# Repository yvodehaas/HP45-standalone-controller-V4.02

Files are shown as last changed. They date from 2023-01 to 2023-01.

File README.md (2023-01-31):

# HP45-standalone-controller-V4.02
HP45 standalone controller V4.02

This github repository is a direct upload of the HP45 Standalone controller V4.02.

This version uses a Teensy 3.5, has all the extra circuits to use DMA for inkjet, and has self testing capabilities. 
A more detailed set of information can be found here: https://ytec3d.com/hp45-controller-v4/

The firmware to run on this board is found here: https://github.com/yvodehaas/HP45-standalone-V4
And the software to control it is found here: https://github.com/yvodehaas/Inkjet-commander
Oasis controller also works on this controller, though it will only work in an Oasis based machine: https://hackaday.io/project/86954-oasis-3dp

This project has been discontinued on my side and is uploaded in the hope that someone else can use it as a template or as is. It is provided without warranty.

The board has a few known issues to keep in mind:
- The reset pulse circuit that resets the TLC59213 using the 74HC123 NEEDS to work. Without this the TLC59213 stays powered. Best case this destroys the HP45 nozzles on the HP45, works case it first destroys the TLC59213, then the Teensy 3.5
- The TLC59213 has a direct connection to the Teensy 3.5. The TLC59213 breaking usually applies the 12V supply to the Teensy 3.5 pins, destroying it.
- The Address testing circuit sometimes gives false negatives. The controller will still print, but while throwing errors.
- The resistor accross the 4017 and 4081 circuit (address circuit) is there to raise the voltage for the nozzle check circuit. The HP45 has pulldown resistors that lowered the voltage on the test circuit sufficiently to stop being able to test.
- Temperature is an indication. The formula was based on 2 printheads while it is known that the HP45 has no accurate temperature sensor. 80C at startup is possible.
- The controller needs 3 pulses to fire all nozzles in an address. This is done 5 primitives, 5 primitives and 4 primitives on each address. This seems to be an issue in the HP45, where too much heat builds up, leading to misfirings. Varying the voltage on the VHD should make this better, but this needs to be calibrated for each printhead.

This list will get appended when more issues are found.

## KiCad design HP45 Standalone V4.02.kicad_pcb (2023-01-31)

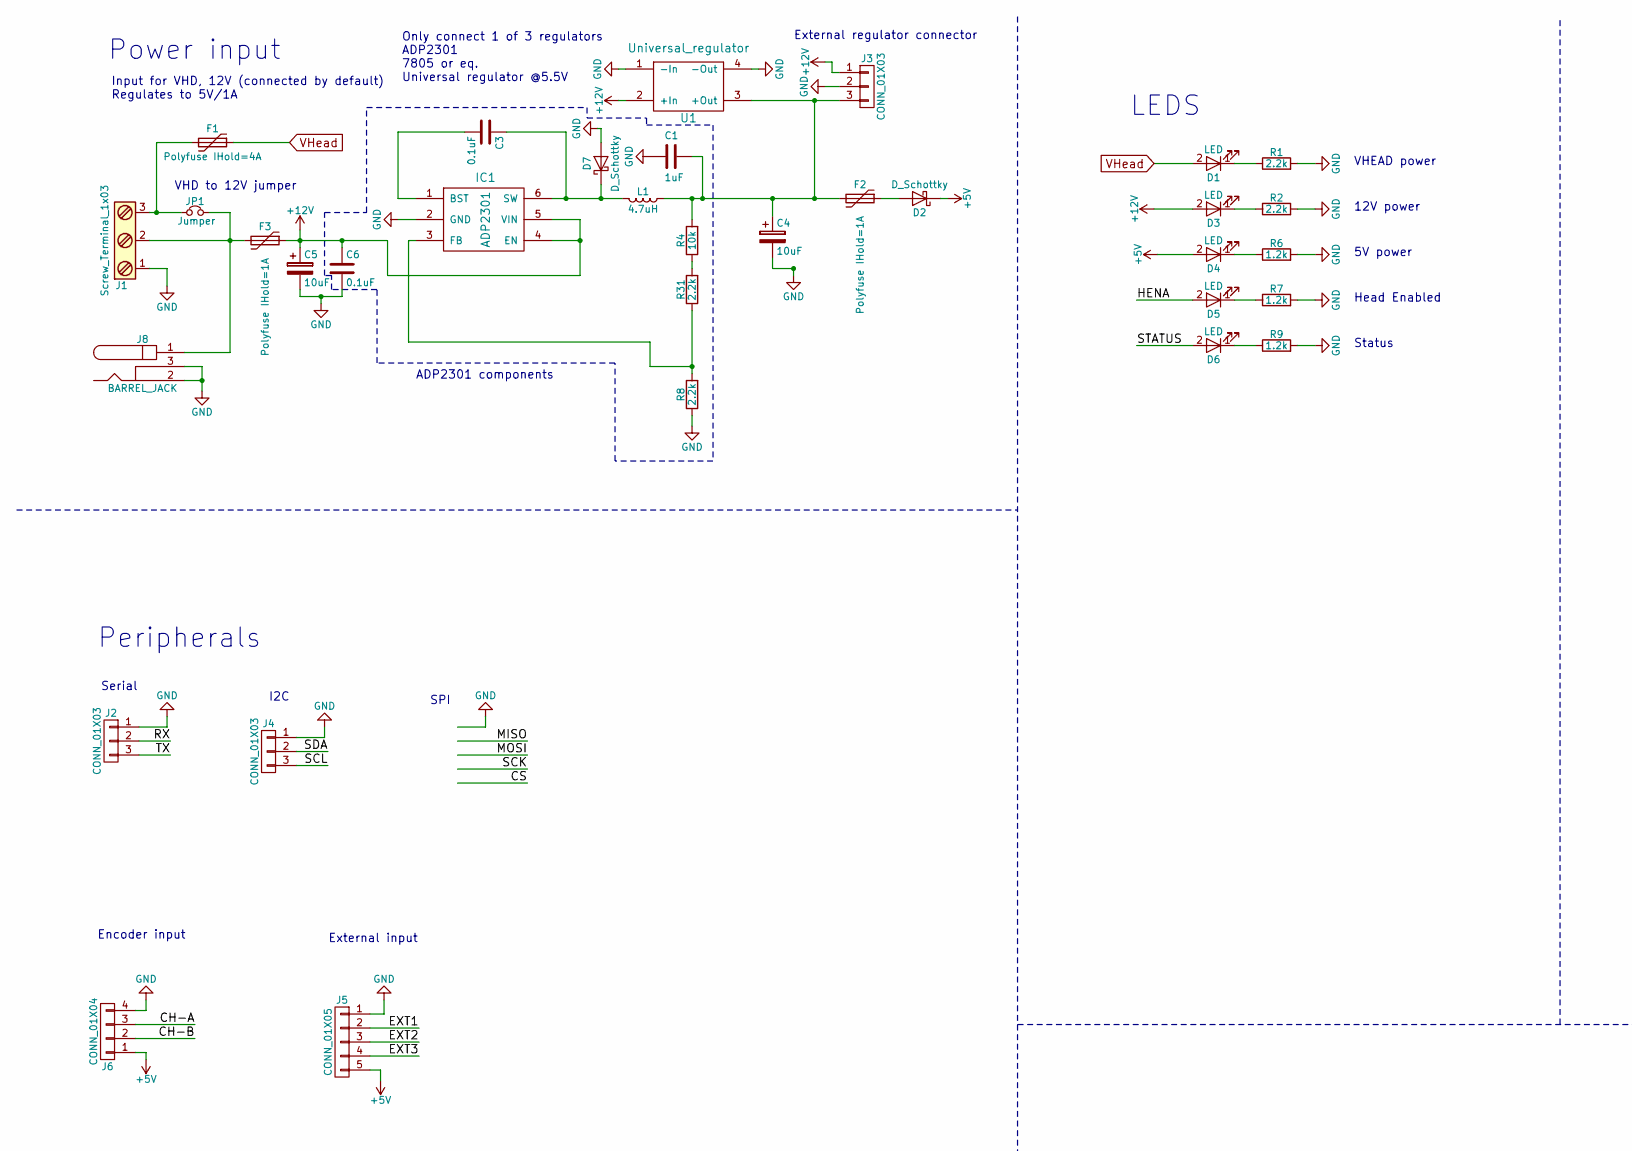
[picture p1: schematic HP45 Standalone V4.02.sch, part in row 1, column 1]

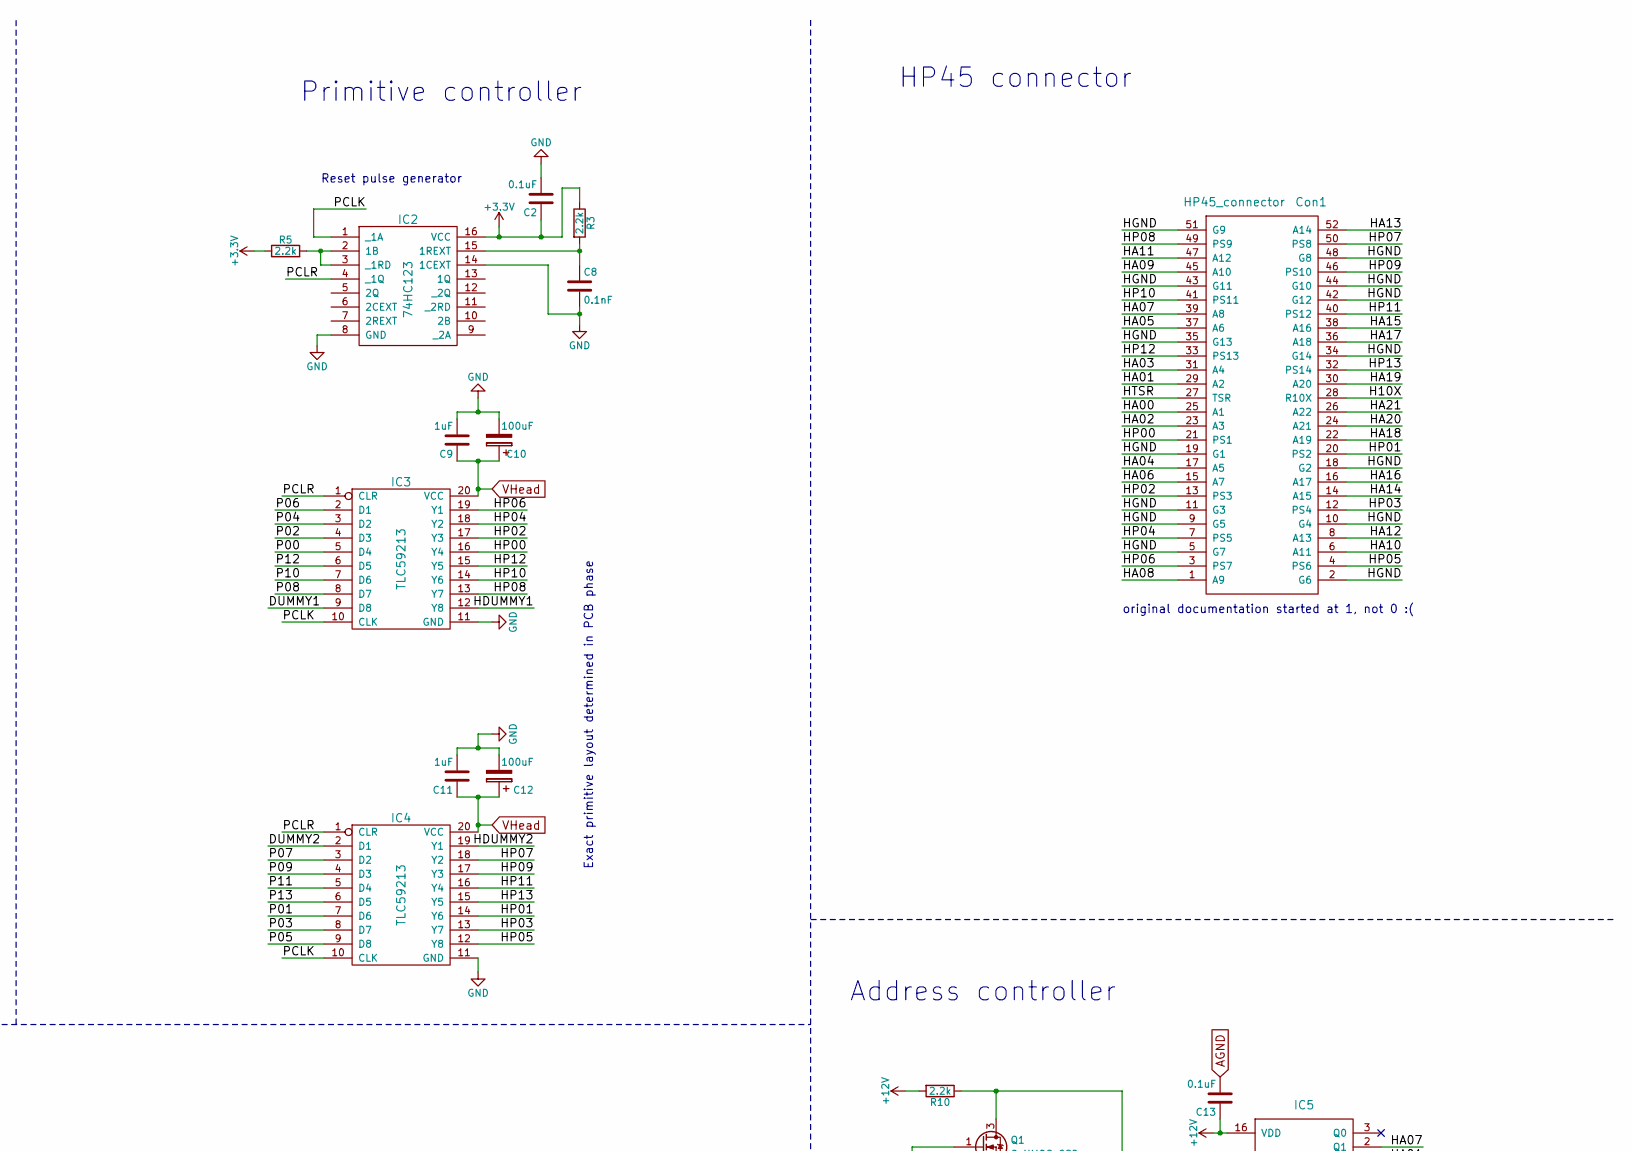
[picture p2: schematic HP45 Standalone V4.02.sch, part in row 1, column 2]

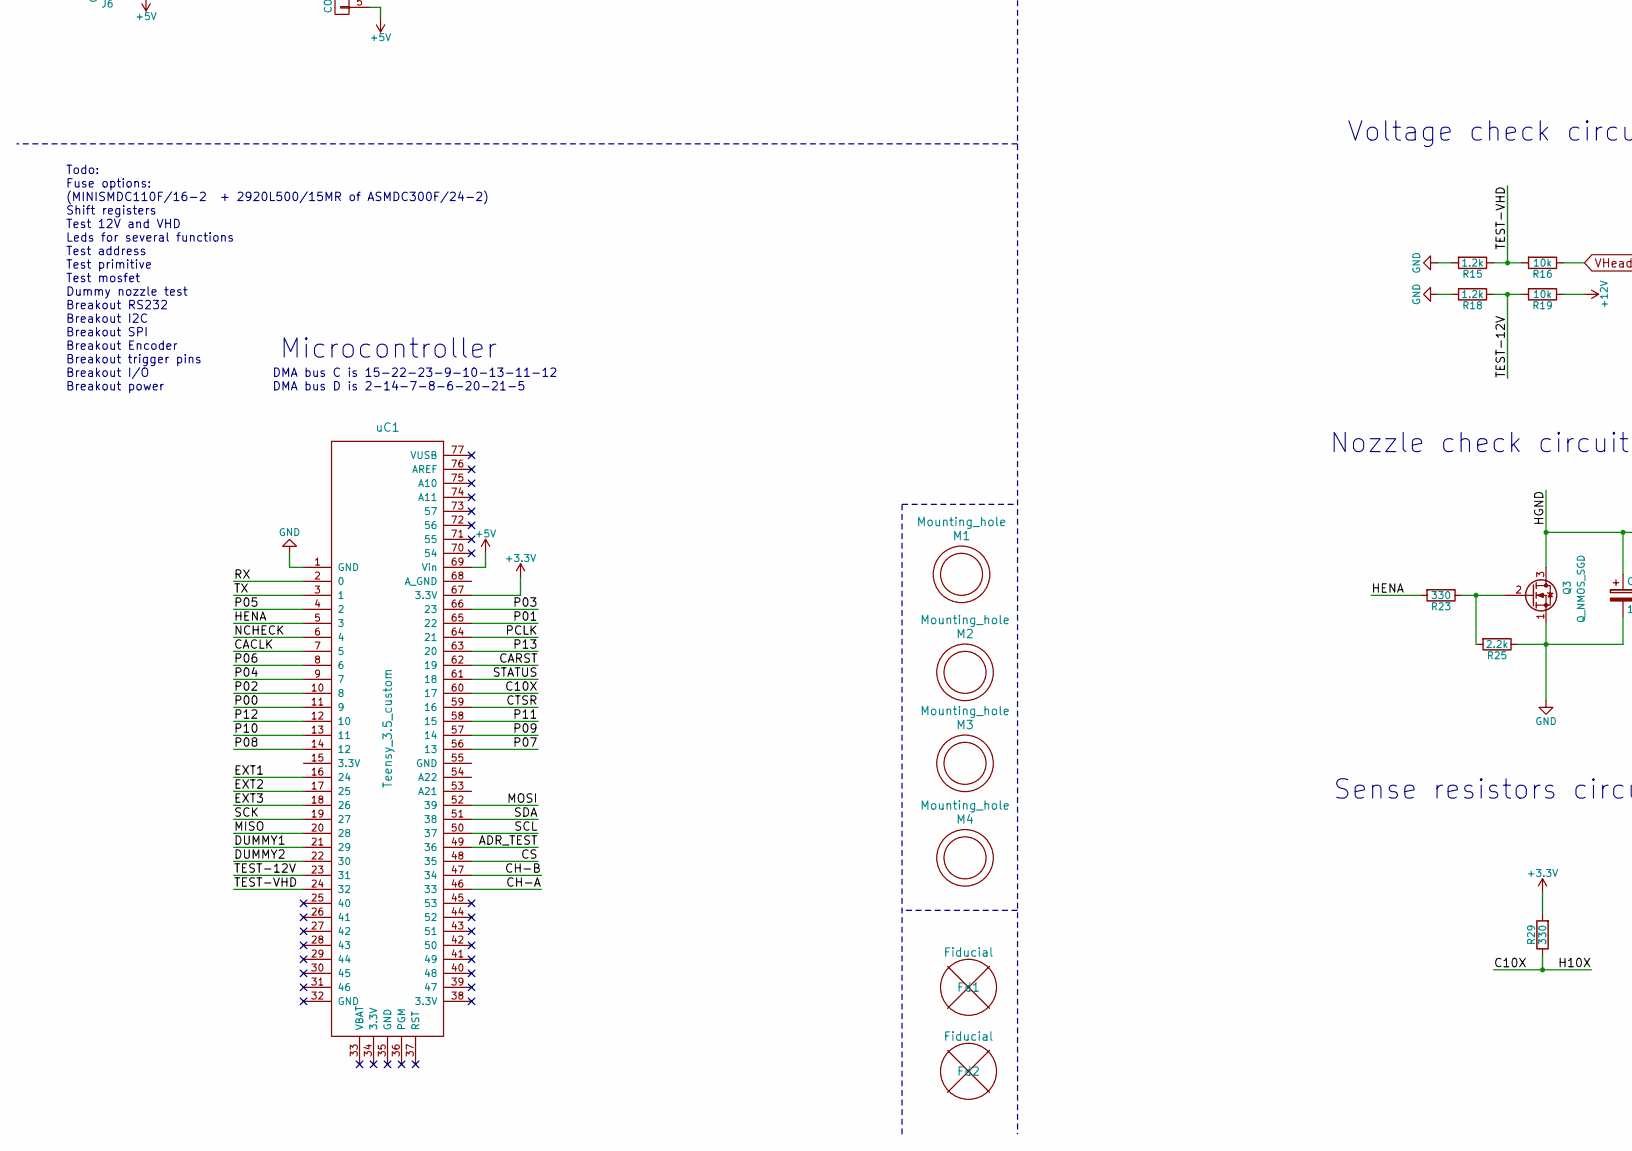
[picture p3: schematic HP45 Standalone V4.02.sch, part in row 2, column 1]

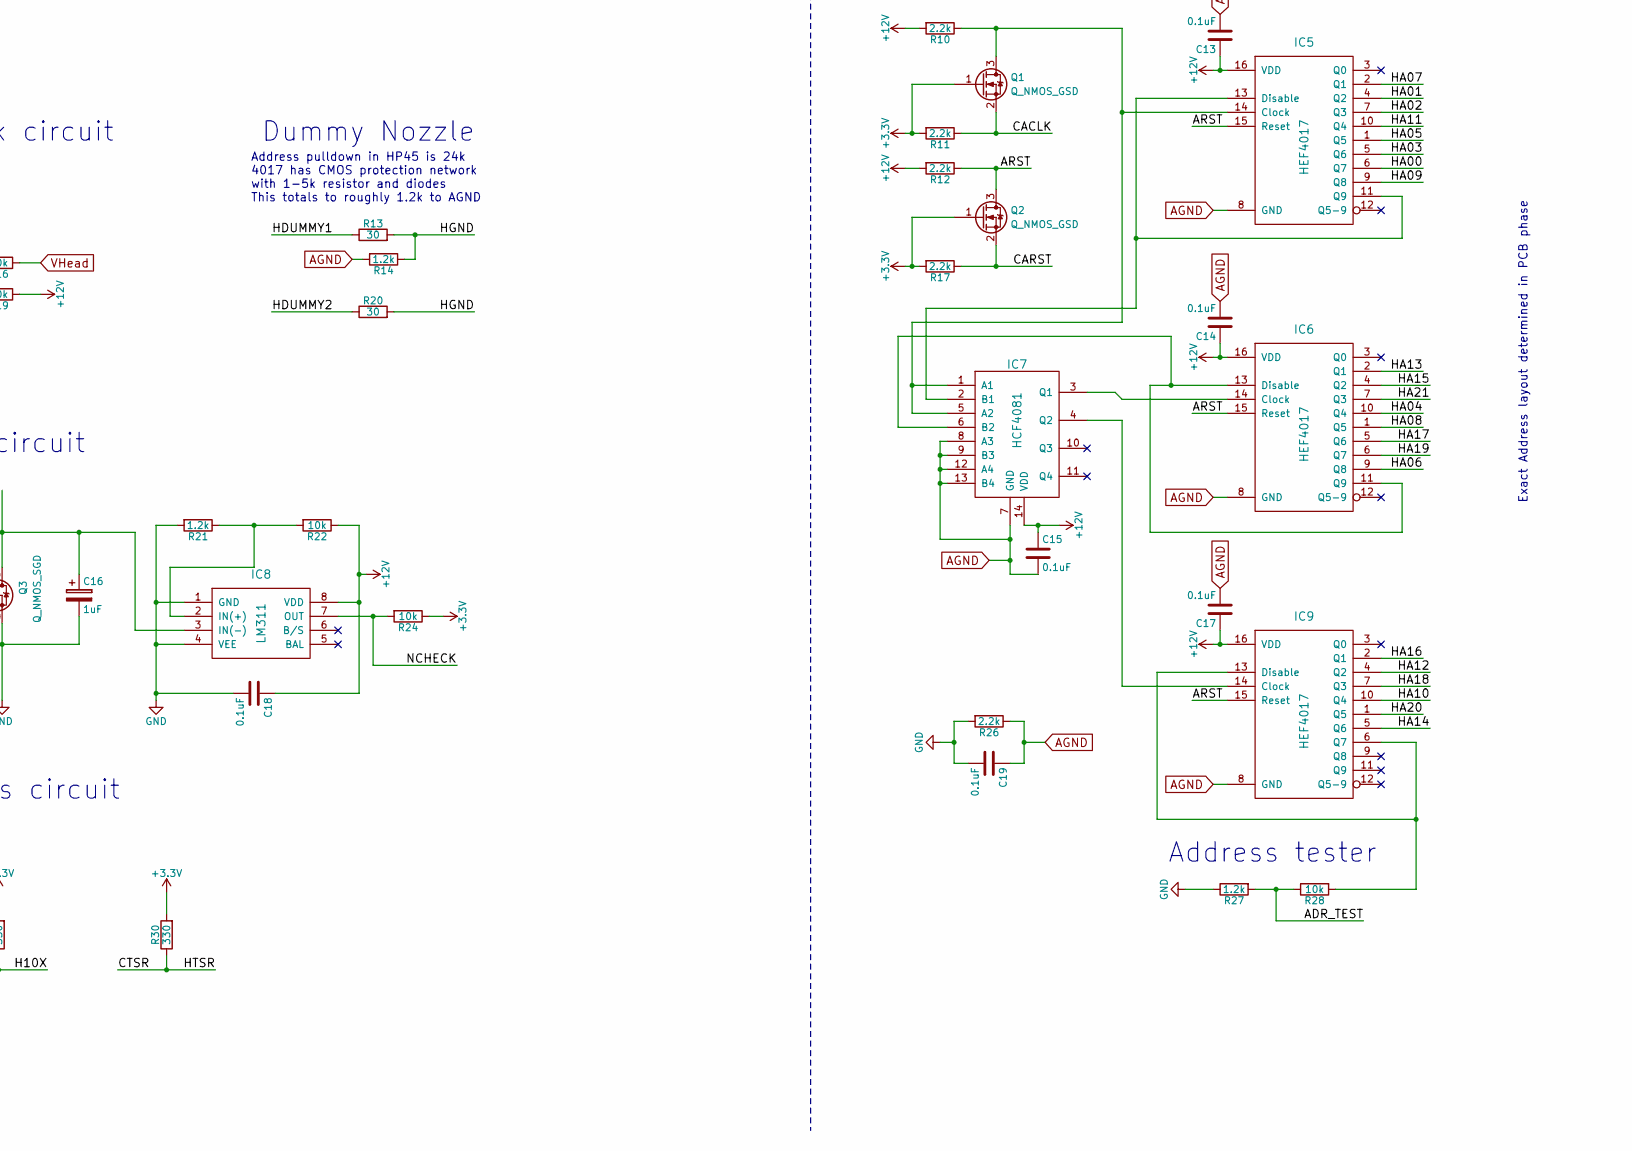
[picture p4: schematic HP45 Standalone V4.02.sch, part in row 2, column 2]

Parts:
C1, C9, C11: 1uF; C_0603
C2, C3, C6, C13, C14, C15, C17, C18, C19: 0.1uF; C_0603
C4, C5: 10uF; CP_Elec_4x5.8
C8: 0.1nF; C_0603
C10, C12: 100uF; CP_Elec_8x10
C16: 1uF; CP_Elec_4x5.8
Con1: HP45_connector; HP45_SMD_connector
D1, D3, D4, D5, D6: LED; LED_0603
D2, D7: D_Schottky; D_SOD-323HE
F1: Polyfuse IHold=4A; Universal_PTC
F2, F3: Polyfuse IHold=1A; R_1812
Fd1, Fd2: Fiducial; Fiducial_1mm_Dia_2mm_Outer
IC1: ADP2301; TSOP-6_1.65x3.05mm_Pitch0.95mm
IC2: 74HC123; TSSOP-16_4.4x5mm_Pitch0.65mm
IC3, IC4: TLC59213; TSSOP-20_4.4x6.5mm_Pitch0.65mm
IC5, IC6, IC9: HEF4017; SSOP-16_4.4x5.2mm_Pitch0.65mm
IC7: HCF4081; TSSOP-14_4.4x5mm_Pitch0.65mm
IC8: LM311; SOIC-8_3.9x4.9mm_Pitch1.27mm
J1: Screw_Terminal_1x03; 3.5mm_screw_terminal
J2, J4: CONN_01X03; JST_XH_B03B-XH-A_03x2.50mm_Straight
J3: CONN_01X03; Pin_Header_Straight_1x03_Pitch2.54mm
J5: CONN_01X05; JST_XH_B05B-XH-A_05x2.50mm_Straight
J6: CONN_01X04; JST_XH_B04B-XH-A_04x2.50mm_Straight
J8: BARREL_JACK
JP1: Jumper; NC_Jumper
L1: 4.7uH; Inductor_Taiyo-Yuden_NR-50xx_HandSoldering
M1, M2, M3, M4: Mounting_hole; MountingHole_3.2mm_M3_Pad_Via
Q1, Q2: Q_NMOS_GSD; SOT-23
Q3: Q_NMOS_SGD; SO-8_PowerPAK
R1, R2, R3, R5, R8, R10, R11, R12, R17, R25, R26, R31: 2.2k; R_0603
R4, R16, R19, R22, R24, R28: 10k; R_0603
R6, R7, R9, R14, R15, R18, R21, R27: 1.2k; R_0603
R13, R20: 30; R_0805
R23, R29, R30: 330; R_0603
U1: Universal_regulator
uC1: Teensy_3.5_custom; Teensy_3.5_edges

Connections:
+3V3: C2.1, IC2.16 (VCC), Q1.1 (G), Q2.1 (G), R3.1, R5.1, R11.2, R17.2, R24.1, R29.2, R30.2, uC1.67 (3.3V)
+5V: D2.1 (K), D4.2 (A), J5.5, J6.1, uC1.69 (Vin)
+12V: C5.1, C6.1, C13.1, C14.1, C15.1, C17.1, C18.1, D3.2 (A), F3.1, IC1.4 (EN), IC1.5 (VIN), IC5.16 (VDD), IC6.16 (VDD), IC7.14 (VDD), IC8.8 (VDD), IC9.16 (VDD), J3.1, R10.2, R12.2, R19.1, R22.1, U1.2 (+In)
/ADR_TEST: R27.2, R28.1, uC1.49 (36)
/ARST: IC5.15 (Reset), IC6.15 (Reset), IC9.15 (Reset), Q2.3 (D), R12.1
/C10X: Con1.28 (R10X), R29.1, uC1.60 (17)
/CACLK: Q1.2 (S), R11.1, uC1.7 (5)
/CARST: Q2.2 (S), R17.1, uC1.62 (19)
/CH-A: J6.3, uC1.46 (33)
/CH-B: J6.2, uC1.47 (34)
/CTSR: Con1.27 (TSR), R30.1, uC1.59 (16)
/DUMMY1: IC3.9 (D8), uC1.21 (29)
/DUMMY2: IC4.2 (D1), uC1.22 (30)
/EXT1: J5.2, uC1.16 (24)
/EXT2: J5.3, uC1.17 (25)
/EXT3: J5.4, uC1.18 (26)
/HA00: Con1.25 (A1), IC5.6 (Q7)
/HA01: Con1.29 (A2), IC5.4 (Q2)
/HA02: Con1.23 (A3), IC5.7 (Q3)
/HA03: Con1.31 (A4), IC5.5 (Q6)
/HA04: Con1.17 (A5), IC6.10 (Q4)
/HA05: Con1.37 (A6), IC5.1 (Q5)
/HA06: Con1.15 (A7), IC6.9 (Q8)
/HA07: Con1.39 (A8), IC5.2 (Q1)
/HA08: Con1.1 (A9), IC6.1 (Q5)
/HA09: Con1.45 (A10), IC5.9 (Q8)
/HA10: Con1.6 (A11), IC9.10 (Q4)
/HA11: Con1.47 (A12), IC5.10 (Q4)
/HA12: Con1.8 (A13), IC9.4 (Q2)
/HA13: Con1.52 (A14), IC6.2 (Q1)
/HA14: Con1.14 (A15), IC9.5 (Q6)
/HA15: Con1.38 (A16), IC6.4 (Q2)
/HA16: Con1.16 (A17), IC9.2 (Q1)
/HA17: Con1.36 (A18), IC6.5 (Q6)
/HA18: Con1.22 (A19), IC9.7 (Q3)
/HA19: Con1.30 (A20), IC6.6 (Q7)
/HA20: Con1.24 (A21), IC9.1 (Q5)
/HA21: Con1.26 (A22), IC6.7 (Q3)
/HDUMMY1: IC3.12 (Y8), R13.1
/HDUMMY2: IC4.19 (Y1), R20.1
/HENA: D5.2 (A), R23.2, uC1.5 (3)
/HGND: C16.1, Con1.2 (G6), Con1.5 (G7), Con1.9 (G5), Con1.10 (G4), Con1.11 (G3), Con1.18 (G2), Con1.19 (G1), Con1.34 (G14), Con1.35 (G13), Con1.42 (G12), Con1.43 (G11), Con1.44 (G10), Con1.48 (G8), Con1.51 (G9), IC8.3 (IN(-)), Q3.3 (D), R13.2, R14.1, R20.2
/HP00: Con1.21 (PS1), IC3.16 (Y4)
/HP01: Con1.20 (PS2), IC4.14 (Y6)
/HP02: Con1.13 (PS3), IC3.17 (Y3)
/HP03: Con1.12 (PS4), IC4.13 (Y7)
/HP04: Con1.7 (PS5), IC3.18 (Y2)
/HP05: Con1.4 (PS6), IC4.12 (Y8)
/HP06: Con1.3 (PS7), IC3.19 (Y1)
/HP07: Con1.50 (PS8), IC4.18 (Y2)
/HP08: Con1.49 (PS9), IC3.13 (Y7)
/HP09: Con1.46 (PS10), IC4.17 (Y3)
/HP10: Con1.41 (PS11), IC3.14 (Y6)
/HP11: Con1.40 (PS12), IC4.16 (Y4)
/HP12: Con1.33 (PS13), IC3.15 (Y5)
/HP13: Con1.32 (PS14), IC4.15 (Y5)
/NCHECK: IC8.7 (OUT), R24.2, uC1.6 (4)
/P00: IC3.5 (D4), uC1.11 (9)
/P01: IC4.7 (D6), uC1.65 (22)
/P02: IC3.4 (D3), uC1.10 (8)
/P03: IC4.8 (D7), uC1.66 (23)
/P04: IC3.3 (D2), uC1.9 (7)
/P05: IC4.9 (D8), uC1.4 (2)
/P06: IC3.2 (D1), uC1.8 (6)
/P07: IC4.3 (D2), uC1.56 (13)
/P08: IC3.8 (D7), uC1.14 (12)
/P09: IC4.4 (D3), uC1.57 (14)
/P10: IC3.7 (D6), uC1.13 (11)
/P11: IC4.5 (D4), uC1.58 (15)
/P12: IC3.6 (D5), uC1.12 (10)
/P13: IC4.6 (D5), uC1.63 (20)
/PCLK: IC2.1 (_1A), IC3.10 (CLK), IC4.10 (CLK), uC1.64 (21)
/PCLR: IC2.4 (_1Q), IC3.1 (CLR), IC4.1 (CLR)
/RX: J2.2, uC1.2 (0)
/SCL: J4.3, uC1.50 (37)
/SDA: J4.2, uC1.51 (38)
/STATUS: D6.2 (A), uC1.61 (18)
/TEST-12V: R18.1, R19.2, uC1.23 (31)
/TEST-VHD: R15.1, R16.2, uC1.24 (32)
/TX: J2.3, uC1.3 (1)
AGND: C13.2, C14.2, C15.2, C17.2, C19.1, IC5.8 (GND), IC6.8 (GND), IC7.7 (GND), IC7.8 (A3), IC7.9 (B3), IC7.12 (A4), IC7.13 (B4), IC9.8 (GND), R14.2, R26.1
GND: C1.2, C2.2, C4.2, C5.2, C6.2, C8.2, C9.2, C10.2, C11.2, C12.2, C16.2, C18.2, C19.2, D7.2 (A), IC1.2 (GND), IC2.8 (GND), IC2.14 (1CEXT), IC3.11 (GND), IC4.11 (GND), IC8.1 (GND), IC8.4 (VEE), J1.1, J2.1, J3.2, J4.1, J5.1, J6.4, J8.2, J8.3, Q3.1 (S), R1.2, R2.2, R6.2, R7.2, R8.1, R9.2, R15.2, R18.2, R21.2, R25.1, R26.2, R27.1, U1.1 (-In), U1.4 (-Out), uC1.1 (GND)
unnamed: C1.1, C4.1, F2.2, J3.3, L1.1, R4.2, U1.3 (+Out)
unnamed: C3.1, D7.1 (K), IC1.6 (SW), L1.2
unnamed: C3.2, IC1.1 (BST)
unnamed: C8.1, IC2.15 (1REXT), R3.2
unnamed: D1.1 (K), R1.1
unnamed: D2.2 (A), F2.1
unnamed: D3.1 (K), R2.1
unnamed: D4.1 (K), R6.1
unnamed: D5.1 (K), R7.1
unnamed: D6.1 (K), R9.1
unnamed: F1.2, J1.3, JP1.1
unnamed: F3.2, J1.2, J8.1, JP1.2
unnamed: IC1.3 (FB), R8.2, R31.1
unnamed: IC2.2 (1B), IC2.3 (_1RD), R5.2
unnamed: IC5.11 (Q9), IC5.13 (Disable), IC7.2 (B1)
unnamed: IC5.14 (Clock), IC7.1 (A1), IC7.5 (A2), Q1.3 (D), R10.1
unnamed: IC6.11 (Q9), IC6.13 (Disable), IC7.6 (B2)
unnamed: IC6.14 (Clock), IC7.3 (Q1)
unnamed: IC7.4 (Q2), IC9.14 (Clock)
unnamed: IC8.2 (IN(+)), R21.1, R22.2
unnamed: IC9.6 (Q7), IC9.13 (Disable), R28.2
unnamed: Q3.2 (G), R23.1, R25.2
unnamed: R4.1, R31.2
VHead: C9.1, C10.1, C11.1, C12.1, D1.2 (A), F1.1, IC3.20 (VCC), IC4.20 (VCC), R16.1

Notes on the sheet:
Address controller
Primitive controller
HP45 connector
Nozzle check circuit
Exact primitive layout determined in PCB phase
Exact Address layout determined in PCB phase
Sense resistors circuit
original documentation started at 1, not 0 :(
VHD to 12V jumper
Power input
Input for VHD, 12V (connected by default) Regulates to 5V/1A
Todo: Fuse options: (MINISMDC110F/16-2 + 2920L500/15MR of ASMDC300F/24-2) Shift registers Test 12V and VHD Leds for several functions Test address Test primitive Test mosfet Dummy nozzle test Breakout RS232 Breakout I2C Breakout SPI Breakout Encoder Breakout trigger pins Breakout I/O Breakout power
LEDS
12V power
5V power
Head Enabled
Status
Serial
Encoder input
Voltage check circuit
Microcontroller
Peripherals
Dummy Nozzle
Address tester
DMA bus C is 15-22-23-9-10-13-11-12 DMA bus D is 2-14-7-8-6-20-21-5
Address pulldown in HP45 is 24k 4017 has CMOS protection network with 1-5k resistor and diodes This totals to roughly 1.2k to AGND
VHEAD power
External input
Reset pulse generator
I2C
SPI
External regulator connector
Only connect 1 of 3 regulators ADP2301 7805 or eq. Universal regulator @5.5V
ADP2301 components

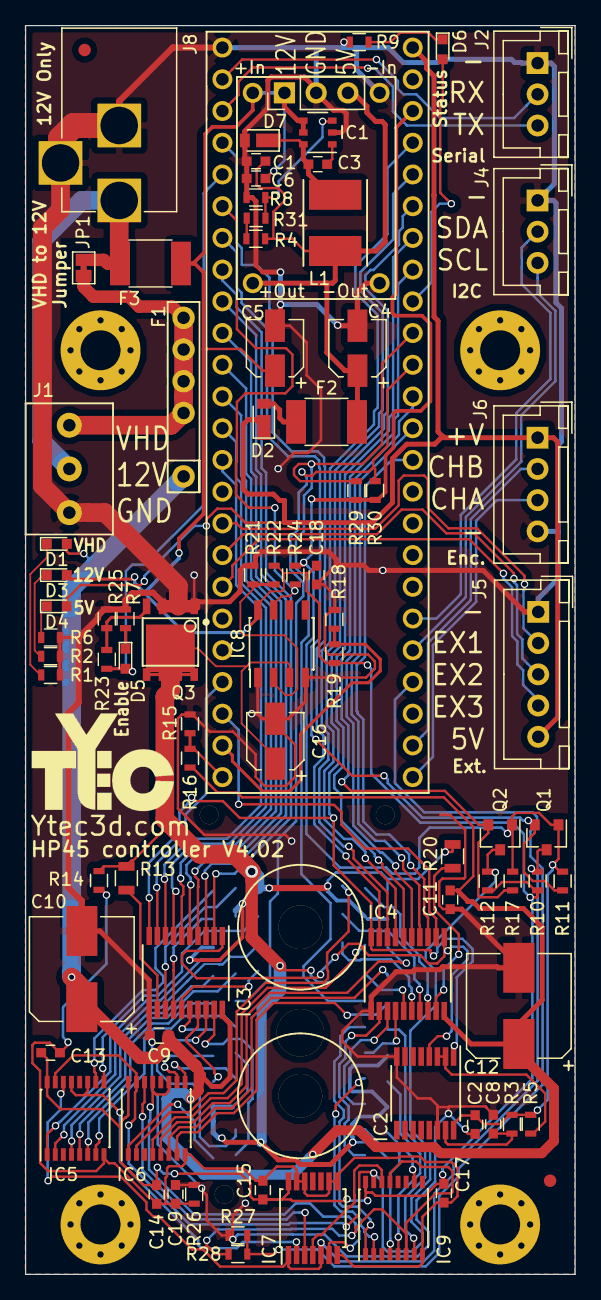
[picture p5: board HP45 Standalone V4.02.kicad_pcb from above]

Board: 2 copper layers, 44.0 x 100.0 mm, 89 parts (1 on the bottom side), 106 nets.
